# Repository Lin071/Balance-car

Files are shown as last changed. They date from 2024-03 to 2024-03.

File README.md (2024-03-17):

# Balance-car

本项目实现了两轮平衡小车，小车可利用遥控（安卓手机串口APP）进行操控（前后左右、灯光、蜂鸣器等）。该小车基于FreeRTOS，主控芯片采用STM32F103C8T6，其他模块包含：

- 一个MPU6050
- 一个OLED显示屏
- 两个蓝牙HC-05模块
- 两个直流减速电机（包含编码器）

PCB是采用Altium Designer设计的四层电路板，包含开关、稳压电路、按键、模块接口等，软件使用keil MDK开发。

# 系统流程

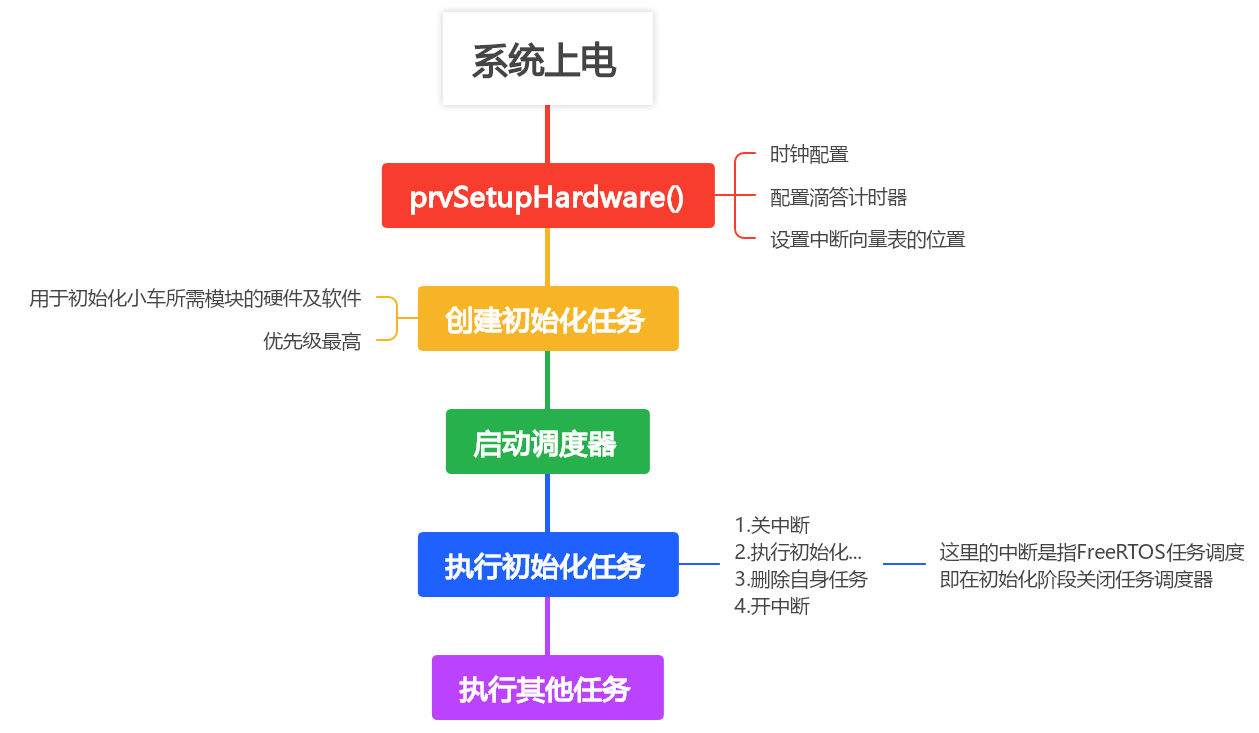
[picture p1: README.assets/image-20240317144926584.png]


小车系统上电后，首先执行FreeRTOS自带的硬件启动函数，包括时钟、中断向量表的地址配置等，使得FreeRTOS可以运行起来。

本项目会先创建一个任务，然后启动调度器。该任务用于初始化小车的各个模块以及创建其他任务，该任务完成后，会自己把自己删掉，起到一个初始化的作用。

- 那为什么要这样做呢？

  - 因为在一些模块的初始化，需要用到延迟函数（例如OLED），然后FreeRTOS已经使用了滴答计时器，这个时候就不好像裸机系统一样利用滴答计时器来计算延迟

  - 虽然说可以使用其他定时器或者纯软件实现延迟函数，但是这毕竟是需要消耗一些资源的，对于资源紧张的MCU来说成本就会增加

  - 正好FreeRTOS自带了ms级任务延迟，所以可以使用 `vTaskDelay(pdMS_TO_TICKS(xxx ms))` 函数来实现ms级延迟

  - 但是利用任务来初始化时一定要注意在任务延迟时，后台会将任务阻塞，为了避免在初始化任务中发生任务调度，需要关闭FreeRTOS的任务调度器

  - 初始化任务服务函数如下：

    ```c
    /***************************************************************************
    *函  数：static void vInitTask(void *pvParameters)
    *功  能：初始化任务，用于初始化小车模块以及创建其他模块
    *参  数：pvParameters 为创建任务时所传递的参数
    *返回值：无
    ***************************************************************************/
    static void vInitTask(void *pvParameters)
    {
    	taskENTER_CRITICAL();	//关闭任务调度
    
    	BaseType_t xReturn;
    	vTaskDelay(pdMS_TO_TICKS( 500UL ));		//先延迟一段时间
    	
    	NVIC_PriorityGroupConfig( NVIC_PriorityGroup_2 ); //设置NVIC中断分组2:2位抢占优先级，2位响应优先级
    
    	/*	相关模块初始化	*/
    	Led_Init();             //=====初始化与 LED 连接的IO
    	Beep_Init();			//=====初始化与 蜂鸣器 连接的IO
    	Key_Init();				//=====按键初始化
    	Oled_Init();			//=====OLED初始化
    	Motor_Init();		    //=====初始化与电机连接的硬件IO接口
    	Encoder_Init();       	//=====初始化编码器A
    	Uart1_init(115200);	    //=====串口1初始化(用于HC-05蓝牙连接上位机显示波形)
    	Uart3_init(115200);     //=====串口3初始化(用于手机遥控)
    	Mpu6050_Init();			//=====MPU6050初始化
    	Key_EXTI_Init();		//=====按键中断初始化
    	MPU6050_EXTI_Init();	//=====MPU6050中断初始化
    	xReturn = Task_Init();	//-----创建其他任务
    	
    	if (xReturn != pdPASS)
    		// 进入这里代表其他任务创建失败
    		OLED_ShowString(0,8,(u8 *)"Task init fail",16);
    
    	vTaskDelete(NULL); 	// 删除自己
    
    	taskEXIT_CRITICAL();	//打开任务调度
    }
    ```

在初始化任务完成之后，系统就会开始调度其他任务进行执行。

# 小车任务

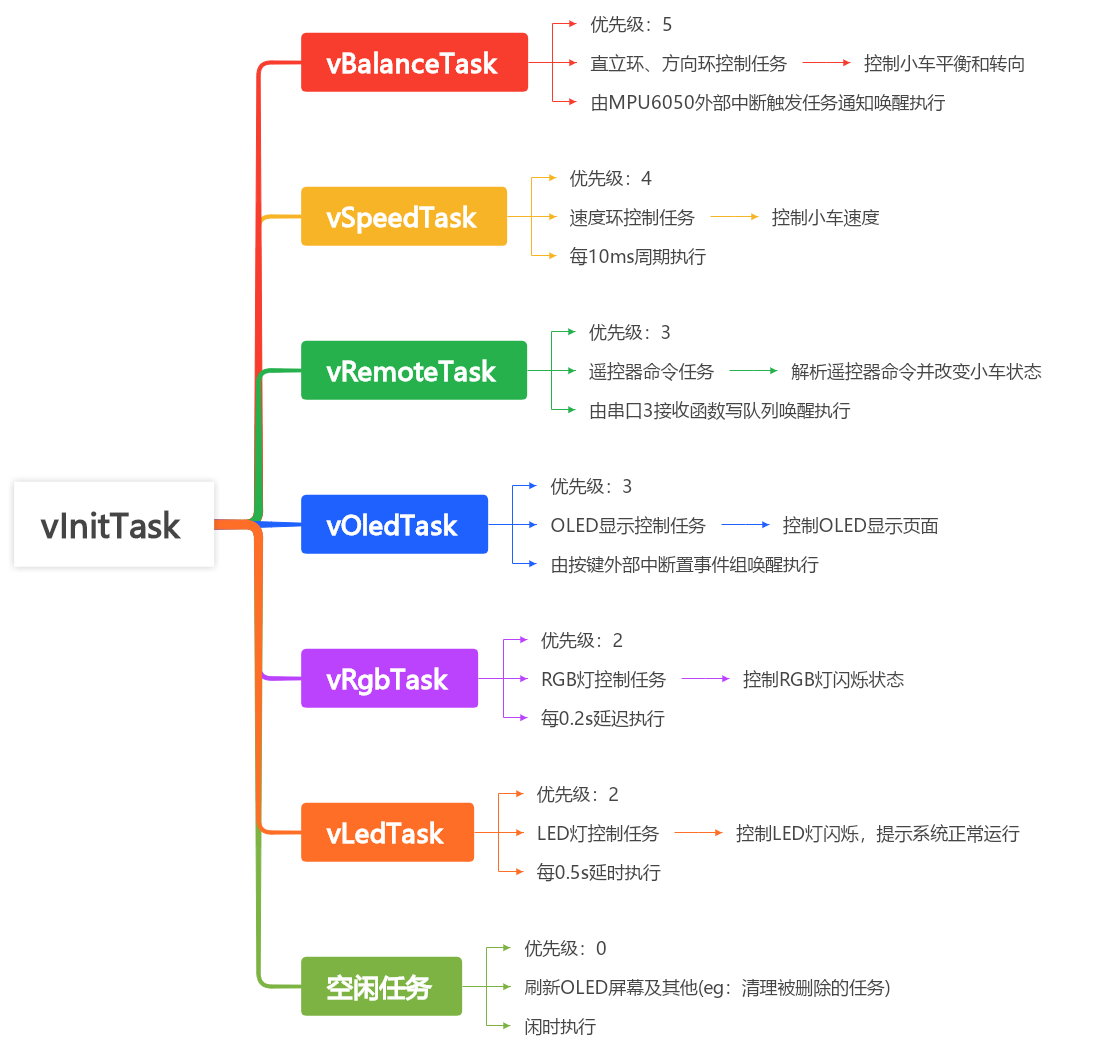
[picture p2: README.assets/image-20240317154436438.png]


本项目一共创建了8个任务，下面将依次介绍：

- `vInitTask`：第一个创建的任务，用于小车各个模块初始化、中断初始化以及创建其他任务，该任务只执行一次，执行完毕后立马删除自身
- `vBalanceTask`：控制小车直立和方向，内部使用任务通知阻塞等待MPU6050外部中断，只有得到了任务通知，该任务才可以执行
- `vSpeedTask`：控制小车速度，周期性获取小车编码器数值，并计算速度环控制输出
- `vRemoteTask`：解析遥控器命令，内部使用队列读阻塞等待，当队列中没有数据时阻塞，有数据时才会执行，队列数据由串口接收服务函数（接收遥控器命令）写入
- `vOledTask`：控制OLED屏幕的显示页面，内部使用事件组阻塞等待，当没有事件发生时阻塞，其中某个时间发生才会执行。事件由两个按键中断函数发出，一个按键代表页面前翻，一个代表页面后翻，即切换页面
- `vRgbTask`：控制RGB灯的状态，延时循环执行，根据用户发送过来的状态切换RGB灯状态（例如：跑马灯、红、黄、闪烁）
- `vLedTask`：控制LED灯翻转，延时循环执行，示意小车正常运行
- 空闲任务：用于CPU闲时处理其他不很重要事情，例如清理已被删除的任务、OLED屏幕刷新

# 任务执行条件

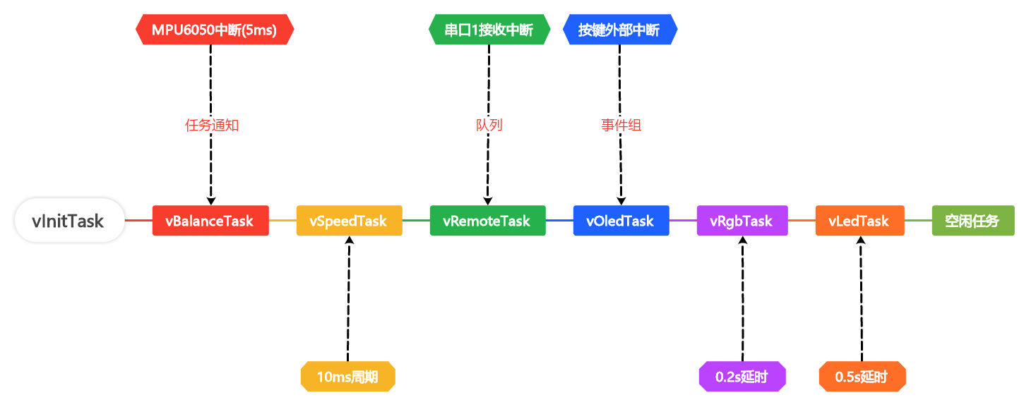
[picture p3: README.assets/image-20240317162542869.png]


# 中断优先级

本项目共用到了两类中断，5个中断：

- 串口1接收中断
- 串口3接收中断
- 按键1外部中断
- 按键2外部中断
- MPU6050数据外部中断

配置NVIC （NVIC的全称是Nested vectoredinterrupt controller，即嵌套向量中断控制器） 分组为 `NVIC_PriorityGroup_2` ，NVIC分组情况如下表所示：

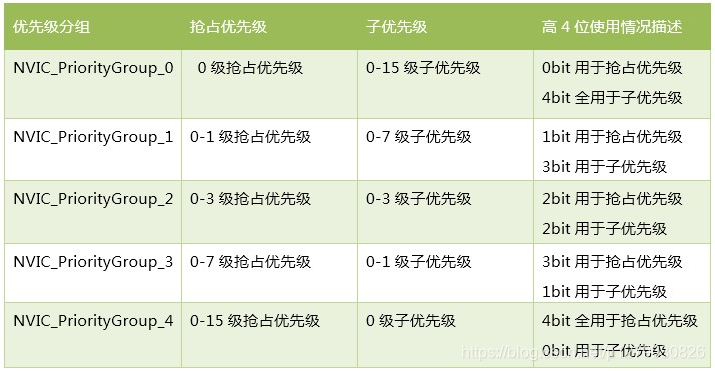
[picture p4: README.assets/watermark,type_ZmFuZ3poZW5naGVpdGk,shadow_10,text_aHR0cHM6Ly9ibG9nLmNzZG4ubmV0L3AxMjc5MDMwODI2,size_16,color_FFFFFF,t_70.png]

本项目各中断优先级配置如下：

| 中断名 | 抢占优先级 | 子优先级 |
| --- | --- | --- |
| MPU6050数据外部中断 | 0 | 1 |
| 按键1外部中断 | 1 | 1 |
| 按键2外部中断 | 1 | 2 |
| 串口1接收中断 | 2 | 1 |
| 串口3接收中断 | 2 | 2 |

另外，对于系统中断（比如：PendSV，SVC，SysTick）等优先级的配置见[FreeRTOS优先级配置说明](https://blog.csdn.net/p1279030826/article/details/103141778)

# 遇到的问题

## MPU6050初始化

- 问题描述：

  - 在初始化MPU6050时，总是会初始化不成功，或者是使用DAP调试器单步调试才能初始化成功，一旦使用电池供电就初始化失败！

- 可能的原因：

  - IIC时序出现问题，因为STM32F103芯片的硬件IIC可能会出现问题，所以本项目使用的是软件IIC，在将信号翻转的过程中，可能需要微秒级延迟一会，但是并没有实现

- 解决办法——实现微秒级延迟，采用方法：

  1. 使用纯软件的方式实现，即在延迟函数中不断进行一定次数循环，以满足特定的延迟时间。但是这种方法需要计算出每个循环所需要的时间，不同单片机的时钟主频不一致很难进行移植，而且延迟不也精准，何况还可能在for循环期间被RTOS任务切换，导致时间更加不准确，故不推荐使用这种方法。

     ```c
     // 实现微秒级延时
     static void delay_us(uint32_t nus)
     {
         uint32_t i;
         uint32_t time = xxx;	//每次循环所占的时间
         nus = nus * time;
         for (i = 0; i < nus; i++) {
             // 做一些其他事
         }
     }
     ```

  2. 使用滴答定时器方式实现微秒级延迟，虽然FreeRTOS是利用滴答定时器实现系统时间以及任务切换等等，但是这并不妨碍我们利用滴答计时器实现微秒级延迟。

     > 参考：https://www.iotword.com/17662.html

     ```c
     // 实现微秒级延时(在这之前一定要保证滴答定时器已经初始化了)
     void delay_us(uint32_t nus)
     {
         uint32_t ticks;
         uint32_t told, tnow, reload, tcnt = 0;
     
         reload = SysTick->LOAD;                    // 获取重装载寄存器值
         ticks = nus * (SystemCoreClock / 1000000); // 计数时间值（即需要延迟的tick数）
         told = SysTick->VAL;                       // 获取当前数值寄存器值（开始时数值）
     
         while (1)
         {
             tnow = SysTick->VAL; // 获取当前数值寄存器值
             if (tnow != told)    // 当前值不等于开始值说明已在计数
             {
                 if (tnow < told) {        // 当前值小于开始数值，说明未计到0
                     tcnt += told - tnow; // 计数值=开始值-当前值
                 } else {                              // 当前值大于开始数值，说明已计到0并重新计数
                     tcnt += reload - tnow + told; // 计数值=重装载值-当前值+开始值  （已从开始值计到0）
                 }
     
                 told = tnow; // 更新开始值
                 if (tcnt >= ticks) {
                     break; // 时间超过/等于要延迟的时间,则退出.
                 }
             }
         }
     }
     
     ```

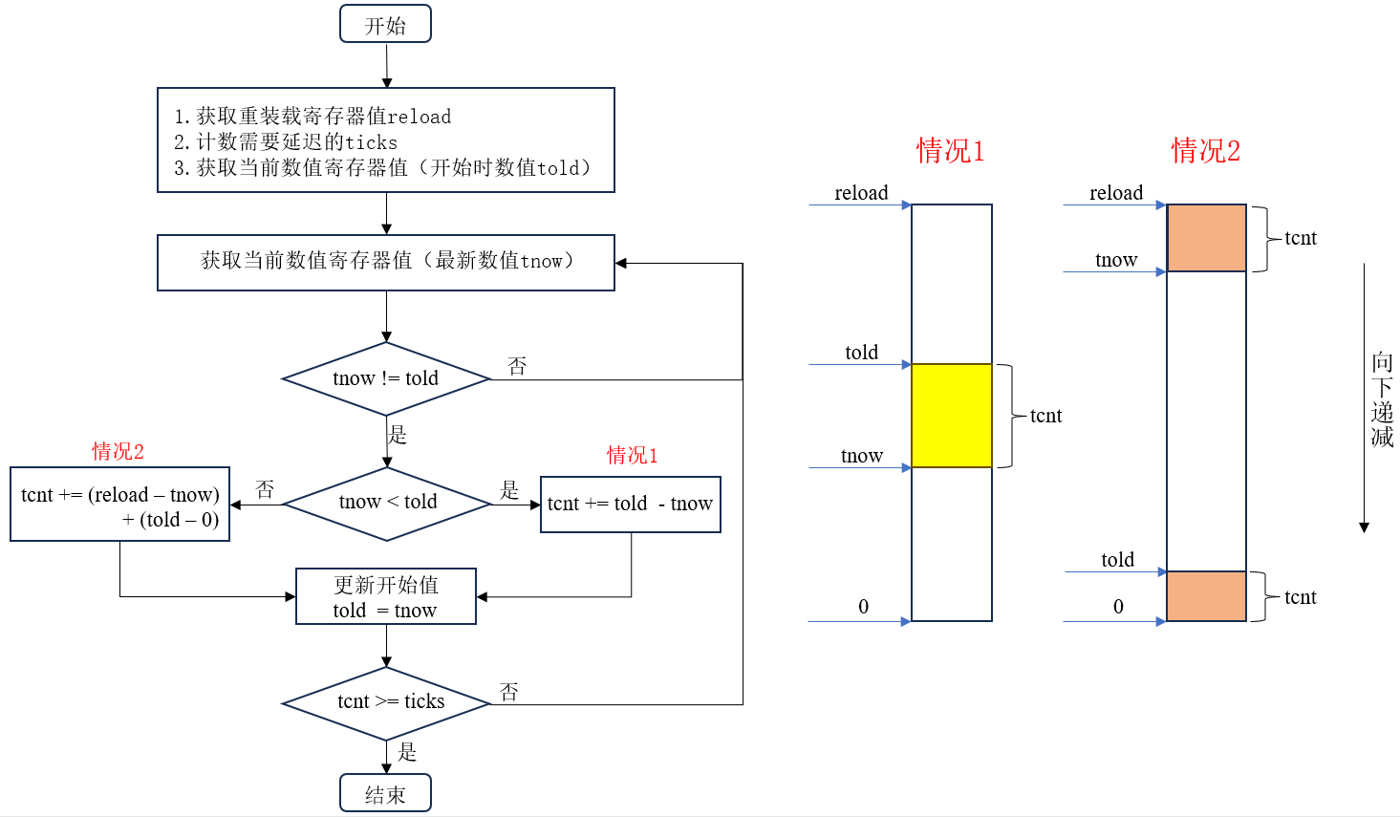
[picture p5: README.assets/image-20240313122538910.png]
     

  3. 使用定时器实现微秒级延迟，这种方法其实与上面第二种方法类似，只不过是换了一种定时器，原理也相同：

     1. 首先计算出需要延迟的时间对应的ticks
     2. 然后重新装载寄存器值
     3. 在循环里不断判断是否超出时间，一旦超出，立即退出

## 外部中断

- 问题描述：

  - 在开发过程中，想要使用按键来操控OLED屏幕显示不同的界面以及调试PID，但是在FreeRTOS中原来的轮循的方式不太行，于是想到使用按键的外部中断来获取按键值，然后在按键外部中断中使用事件组更改相应按键标志位，但是又和MPU6050的外部中断引脚共用了同一个外部中断线（EXTI_Line5）

  - 在STM32F103系列中，外部中断的共用资源主要包括：

    1. 不同端口、同一pin口，共用一个中断线：如PA1、PB1、PC1共用外部中断线1——EXTI_Line1，但是不可以同时使用
    2. 不同pin口、同一端口：这个都不用说，PA1、PA2、PA3这些共用的是同一个端口寄存器之类的
    3. 同一pin口共用一个中断线，但16个中断线却只共用7个中断服务函数：其中中断线EXTI_Line0-4独立拥有一个中断服务，中断线5-9共用一个中断服务函数，中断线10-15共用一个中断服务函数

    > [stm32共用外部中断线问题](https://blog.csdn.net/m0_65346989/article/details/129588667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)

  - 所以不可以同时使用 PA5(按键) 和 PB5(MPU6050) 来作为EXTI_Line5的外部中断

- 解决方案：

  - 只使用其中两个按键用于翻转OLED页面，去除原先的主页面，直接进入第一页面，然后根据按键切换上下页面
  - 至于PID等参数的调试，使用串口连接蓝牙，然后与手机连接，利用串口调试助手软件来更改PID的系数，以及控制小车

## 中断函数使用事件组

- 问题描述：

  - 这个问题是上面第二个问题的进一步延伸。使用其中两个按键来作为外部中断，一个按键按下表示OLED屏幕页面往前翻一页，另一个按键按下表示OLED屏幕往后翻一页
  - 为了更好地利用CPU，创建了一个空闲任务，在空闲任务不断刷新OLED屏幕，然后另外创建一个OLED控制任务，使用事件组来实现屏幕页面的切换
  - 当没有按键按下时，OLED屏幕控制任务处于阻塞态（即没有事件发生），当有时间发生时，判断是哪个事件（页面前翻或者后翻），根据事件类型来改变显示页面（改变函数指针）
  - 在按键中断中需要使用事件组发送事件，因为是外部中断属于ISR，所以需要使用 `xEventGroupSetBitsFromISR` 函数，但是编译的时候出现报错：未定义 `xTimerPendFunctionCallFromISR` 

- 解决方案：

  - 需要在 `FreeRTOSConfig.h` 定义以下：

    ```c
    #define INCLUDE_xEventGroupSetBitFromISR    1
    #define INCLUDE_xTimerPendFunctionCall  	1
    #define configUSE_TIMERS                	1
    ```

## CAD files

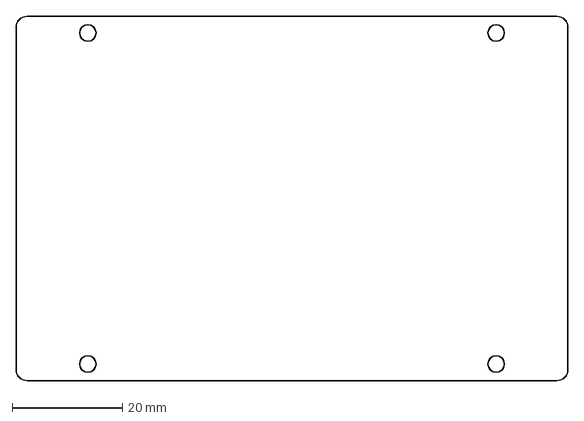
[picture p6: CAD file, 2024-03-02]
Pcb/板子形状.dxf
100.0 x 66.0 mm

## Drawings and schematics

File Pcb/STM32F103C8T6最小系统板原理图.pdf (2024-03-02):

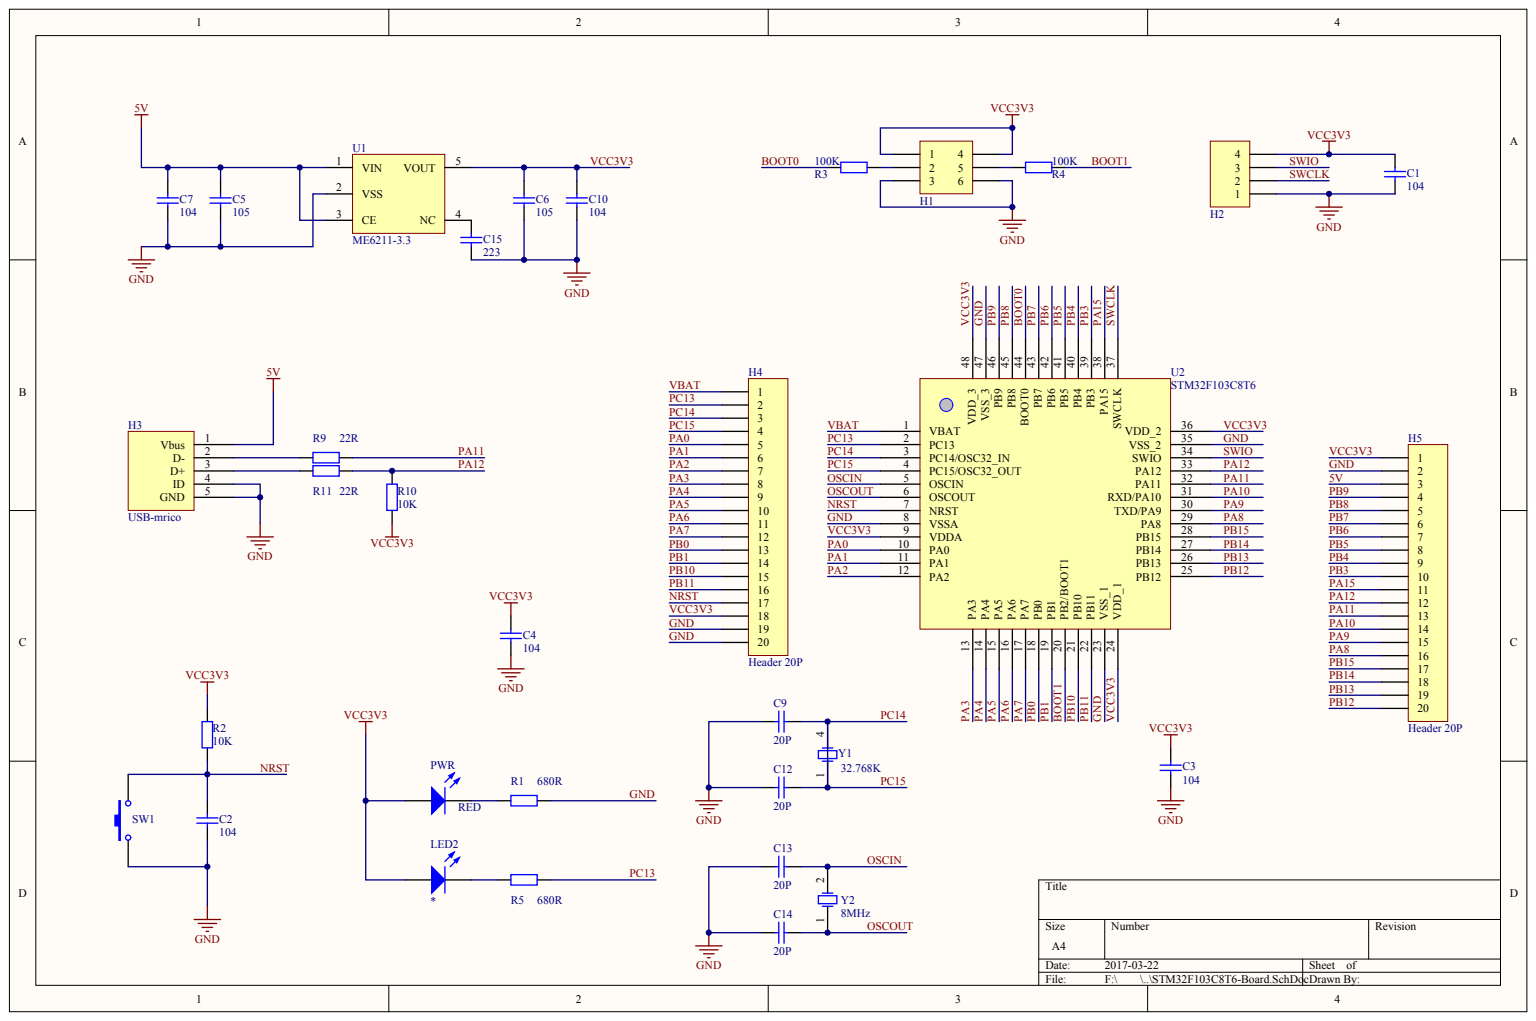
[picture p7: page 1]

VSS 2

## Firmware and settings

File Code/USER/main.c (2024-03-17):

/***********************************************************************/
//		    程序说明
//此程序用于：两轮平衡小车
//所用MCU芯片：STM32F103C8T6
//作者：071
//
/***********************************************************************/

#include "stm32f10x_rcc.h"

#include "FreeRTOS.h"
#include "timers.h"
#include "task.h"

#include "sys.h"
#include "led.h"
#include "beep.h"
#include "key.h"
#include "motor.h"
#include "encoder.h"
#include "oled.h"
#include "remote.h"
#include "control.h"
#include "mpu6050.h"




/* 硬件初始化函数声明 */
static void prvSetupHardware( void );
/*-----------------------------------------------------------*/



/***************************************************************************
*函  数：static void vInitTask(void *pvParameters)
*功  能：初始化任务，用于初始化小车模块以及创建其他模块
*参  数：pvParameters 为创建任务时所传递的参数
*返回值：无
***************************************************************************/
static void vInitTask(void *pvParameters)
{
	taskENTER_CRITICAL();	//关闭任务调度

	BaseType_t xReturn;
	vTaskDelay(pdMS_TO_TICKS( 500UL ));		//先延迟一段时间
	
	NVIC_PriorityGroupConfig( NVIC_PriorityGroup_2 ); //设置NVIC中断分组2:2位抢占优先级，2位响应优先级

	/*	相关模块初始化	*/
	Led_Init();             //=====初始化与 LED 连接的IO
	Beep_Init();			//=====初始化与 蜂鸣器 连接的IO
	Key_Init();				//=====按键初始化
	Oled_Init();			//=====OLED初始化
	Motor_Init();		    //=====初始化与电机连接的硬件IO接口
	Encoder_Init();       	//=====初始化编码器A
	Uart1_init(115200);	    //=====串口1初始化(用于HC-05蓝牙连接上位机显示波形)
	Uart3_init(115200);     //=====串口3初始化(用于手机遥控)
	Mpu6050_Init();			//=====MPU6050初始化
	Key_EXTI_Init();		//=====按键中断初始化
	MPU6050_EXTI_Init();	//=====MPU6050中断初始化
	xReturn = Task_Init();	//-----创建其他任务
	
	if (xReturn != pdPASS)
		// 进入这里代表其他任务创建失败
		OLED_ShowString(0,8,(u8 *)"Task init fail",16);

	vTaskDelete(NULL); 	// 删除自己

	taskEXIT_CRITICAL();	//打开任务调度
}



int main( void )
{
	BaseType_t xReturn;

 	/* RTOS所需基础硬件初始化 */
	prvSetupHardware();
	
  	/* 创建最初始的任务—————用于初始化小车其他模块以及创建其他任务 */
	xReturn = xTaskCreate(vInitTask, "InitTask", 500, NULL, 10, NULL);
	if (xReturn == pdPASS)
	{
		/* 启动调度器 */
		vTaskStartScheduler();
	}
		
	/* 如果程序运行到了这里就表示出错了, 一般是内存不足 */
	RGB_LED_Red();	//RGB红灯亮起
	BEEP_ON;		//蜂鸣器常鸣
	
	return 0;
}

/*-----------------------------------------------------------*/


/*-----------------------------------------------------------*/
static void prvSetupHardware( void )
{
	/* RCC（Reset and Clock Control）复位与时钟控制	Start with the clocks in their expected state. */
	RCC_DeInit();

	/* Enable HSE (high speed external clock). */
	RCC_HSEConfig( RCC_HSE_ON );

	/* Wait till HSE is ready. */
	while( RCC_GetFlagStatus( RCC_FLAG_HSERDY ) == RESET )
	{
	}

	/* 2 wait states required on the flash. */
	*( ( unsigned long * ) 0x40022000 ) = 0x02;

	/* HCLK = SYSCLK */
	RCC_HCLKConfig( RCC_SYSCLK_Div1 );

	/* PCLK2 = HCLK */
	RCC_PCLK2Config( RCC_HCLK_Div1 );

	/* PCLK1 = HCLK/2 */
	RCC_PCLK1Config( RCC_HCLK_Div2 );

	/* PLLCLK = 8MHz * 9 = 72 MHz. */
	RCC_PLLConfig( RCC_PLLSource_HSE_Div1, RCC_PLLMul_9 );

	/* Enable PLL. */
	RCC_PLLCmd( ENABLE );

	/* Wait till PLL is ready. */
	while(RCC_GetFlagStatus(RCC_FLAG_PLLRDY) == RESET)
	{
	}

	/* Select PLL as system clock source. */
	RCC_SYSCLKConfig( RCC_SYSCLKSource_PLLCLK );

	/* Wait till PLL is used as system clock source. */
	while( RCC_GetSYSCLKSource() != 0x08 )
	{
	}

	/* SPI2 Periph clock enable */
	RCC_APB1PeriphClockCmd( RCC_APB1Periph_SPI2, ENABLE );

	/* Configure HCLK clock as SysTick clock source. */
	SysTick_CLKSourceConfig( SysTick_CLKSource_HCLK );

	/* Set the Vector Table base address at 0x08000000 */
	NVIC_SetVectorTable( NVIC_VectTab_FLASH, 0x0 );	
}
/*-----------------------------------------------------------*/

#ifdef  DEBUG
/* Keep the linker happy. */
void assert_failed( unsigned char* pcFile, unsigned long ulLine )
{
	for( ;; )
	{
	}
}
#endif

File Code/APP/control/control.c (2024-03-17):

#include "control.h"

#include "FreeRTOS.h"
#include "event_groups.h"
#include "queue.h"


#include "led.h"
#include "mpu6050.h"
#include "motor.h"
#include "encoder.h"
#include "inv_mpu.h"
#include "oled.h"
#include "gui.h"
#include "remote.h"


// ==定义相关全局变量
PID balancePid, directionPid, speedPid;
float pitch, roll, yaw;
short gx, gy, gz;

// ===定义相关外部所需句柄
TaskHandle_t xBalanceTaskHandle;    // 直立环任务句柄
EventGroupHandle_t xEventGroup;     // 事件组句柄 
QueueHandle_t xQueue;               // 队列句柄


// ==定义任务句柄
static TaskHandle_t xLedTaskHandle;
static TaskHandle_t xRgbTaskHandle;
static TaskHandle_t xOledTaskHandle;
static TaskHandle_t xRemoteTaskHandle;
static TaskHandle_t xSpeedTaskHandle;



/***************************************************************************
*函  数：static void parameterInit(void)
*功  能：PID等参数初始化
*参  数：无
*返回值：无
***************************************************************************/
static void parameterInit(void)
{
    // PID系数初始化
    balancePid.expect = -7.5f;
    balancePid.Kp = 465.0f;       // 0 ~ 700 
    balancePid.Ki = 0.0f;
    balancePid.Kd = -0.55f;

    directionPid.expect = 0;
    directionPid.Kp = 0.65f;
    directionPid.Ki = 0.0f;
    directionPid.Kd = 0.0f;

    speedPid.expect = 0;
    speedPid.Kp = 13.0f;
    speedPid.Ki = 0.065f;
    speedPid.Kd = 0.0f;
}


/***************************************************************************
*函  数：void vApplicationIdleHook(void)
*功  能：空闲任务钩子函数————(优先级最低：0     该任务不可以阻塞)
        1、处理被删除的任务
        2、刷新OLED屏幕
*参  数：pvParameters 为创建任务时所传递的参数
*返回值：无
***************************************************************************/
void vApplicationIdleHook(void)
{
    OLED_Clear();
    pPage();        // 刷新OLED屏幕
}


/***************************************************************************
*函  数：static void vLedTask(void *pvParameters)
*功  能：LED灯任务，闪烁LED灯，提示小车正常运行
*参  数：pvParameters 为创建任务时所传递的参数
*返回值：无
***************************************************************************/
static void vLedTask(void *pvParameters)
{
    const TickType_t xDelayTicks = pdMS_TO_TICKS(500UL);
    uint8_t cnt = 0;
    
    while(1)
    {
        cnt++;
        if(cnt%2 == 0)      // 翻转LED
            LED_OFF;
        else
            LED_ON;
        
        /* 延时 */
        vTaskDelay(xDelayTicks);
    }
}



/***************************************************************************
*函  数：static void vRgbTask(void *pvParameters)
*功  能：RGB灯任务，控制RGB灯的行为，使小车更具趣味性
*参  数：pvParameters 为创建任务时所传递的参数
*返回值：无
***************************************************************************/
static void vRgbTask(void *pvParameters)
{
    const TickType_t xDelayTicks = pdMS_TO_TICKS(200UL);
    
    while(1)
    {
        // 根据rgbState标志位选择RGB状态
        switch(remoteState.rgbState)
        {
            case RGB_OFF:
                RGB_LED_Off();
                break;
            case RGB_FLY:
                RGB_LED_FLY();
                break;
            case RGB_RUNNING:
                RGB_LED_Runing();
                break;
            case RGB_RED:
                RGB_LED_Red();
                break;
            case RGB_BLUE:
                RGB_LED_Blue();
                break;
            case RGB_YELLOW:
                RGB_LED_Yellow();
                break;
            case RGB_WHITE:
                RGB_LED_White();
                break;     
        }

        /* 延时 */
        vTaskDelay(xDelayTicks);
    }
}



/***************************************************************************
*函  数：static void vOledTask(void *pvParameters)
*功  能：OLED显示控制任务，用于控制OLED显示的内容
*参  数：pvParameters 为创建任务时所传递的参数
*返回值：无
***************************************************************************/
static void vOledTask(void *pvParameters)
{
    const TickType_t xDelayTicks = pdMS_TO_TICKS(20UL);
    int8_t i = 0;
    EventBits_t xReturnBit;
    Page_Init();    // 初始化屏幕显示页
    
    while(1)
    {
        /* 延时 */
        vTaskDelay(xDelayTicks);

        /* 等待某一个按键，获取事件后清除标志位，无限期阻塞 */
		xReturnBit = xEventGroupWaitBits(xEventGroup, UP|DOWN, pdTRUE, pdFALSE, portMAX_DELAY);

        // 根据返回值判断哪个按键按下
        if (xReturnBit == UP)
        {
            i--;
            i = i < 0 ? 0 : i;      // 限幅
        } else if (xReturnBit == DOWN)
        {
            i++;
            i = i > (ARR_SIZE-1) ? (ARR_SIZE-1) : i;    // 限幅
        }

        pPage = pageFunctions[i];   // 更新页面
    }
}


/***************************************************************************
*函  数：static void vRemoteTask(void *pvParameters)
*功  能：解析遥控命令任务，等待串口3发送数据至队列，不断读取队列数据
*参  数：pvParameters 为创建任务时所传递的参数
*返回值：无
***************************************************************************/
static void vRemoteTask(void *pvParameters)
{
    uint8_t receivedValue;
    BaseType_t xStatus;

    while(1)
    {
        /* 读取从手机遥控端发送过来的消息，即读取队列
         * 从 xQueue 队列中读取数据至 receivedValue 变量，如果队列没有数据，则无限阻塞
         */
        xStatus = xQueueReceive( xQueue, &receivedValue, portMAX_DELAY);

        // 判断是否读到了数据
        if (xStatus == pdPASS)
        {   
            // 带入解析
            Bluetooth_Receive_Parsing(receivedValue);
        }
    }
}



/***************************************************************************
*函  数：static void vBalanceTask(void *pvParameters)
*功  能：直立环控制任务
*参  数：pvParameters 为创建任务时所传递的参数
*返回值：无
***************************************************************************/
static void vBalanceTask(void *pvParameters)
{
    parameterInit();

    while(1)
    {
        /* 阻塞等待MPU6050中断任务通知，被通知后将通知值清零 */
        ulTaskNotifyTake(pdTRUE, portMAX_DELAY);

        MPU_Get_Gyroscope(&gx, &gy, &gz);         //===得到角速度的数据
        mpu_dmp_get_data(&pitch, &roll, &yaw);    //===得到欧拉角（姿态角）的数据

        // 直立环代码...
        balancePid.error = balancePid.expect - pitch;
        balancePid.out = (int16_t)(balancePid.Kp*balancePid.error + balancePid.Kd*gy);

        // 方向环代码...
        directionPid.error = directionPid.expect - gz;
        directionPid.out = (int16_t)(directionPid.Kp*directionPid.error);

        /* 改变左右两轮占空比 */
        // setMotorPwm(balancePid.out + speedPid.out - directionPid.out, balancePid.out + speedPid.out + directionPid.out);
        setMotorPwm(0, 0);
    }
}
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

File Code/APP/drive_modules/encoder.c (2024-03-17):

#include "encoder.h"

#include <stdio.h>
#include <stdint.h>

#include "stm32f10x_tim.h"
#include "stm32f10x_gpio.h"
#include "stm32f10x_rcc.h"

#include "control.h"


/**************************************************************************
函数功能：把TIM2初始化为编码器接口模式（读取左车轮编码速度）
入口参数：无
返回  值：无
**************************************************************************/
static void A_Encoder_Init(void)
{
	TIM_TimeBaseInitTypeDef TIM_TimeBaseStructure;  
	TIM_ICInitTypeDef TIM_ICInitStructure;  
	GPIO_InitTypeDef GPIO_InitStructure;
	RCC_APB1PeriphClockCmd(RCC_APB1Periph_TIM2, ENABLE);	//使能定时器2的时钟
	RCC_APB2PeriphClockCmd(RCC_APB2Periph_GPIOA, ENABLE);	//使能PA端口时钟
		
	GPIO_InitStructure.GPIO_Pin = GPIO_Pin_0|GPIO_Pin_1;	//端口配置(PA0\PA1)
	GPIO_InitStructure.GPIO_Mode = GPIO_Mode_IN_FLOATING; 	//浮空输入
	GPIO_Init(GPIOA, &GPIO_InitStructure);					//根据设定参数初始化GPIOA
	
	TIM_TimeBaseStructInit(&TIM_TimeBaseStructure);
	TIM_TimeBaseStructure.TIM_Prescaler = 0x0; // 预分频器
	TIM_TimeBaseStructure.TIM_Period = ENCODER_TIM_PERIOD; 		//设定计数器自动重装值
	TIM_TimeBaseStructure.TIM_ClockDivision = TIM_CKD_DIV1;		//选择时钟分频：不分频
	TIM_TimeBaseStructure.TIM_CounterMode = TIM_CounterMode_Up;	//TIM向上计数  
	TIM_TimeBaseInit(TIM2, &TIM_TimeBaseStructure);
	TIM_EncoderInterfaceConfig(TIM2, TIM_EncoderMode_TI12, TIM_ICPolarity_Rising, TIM_ICPolarity_Rising);	//使用编码器模式3
	TIM_ICStructInit(&TIM_ICInitStructure);
	TIM_ICInitStructure.TIM_ICFilter = 10;
	TIM_ICInit(TIM2, &TIM_ICInitStructure);
	TIM_ClearFlag(TIM2, TIM_FLAG_Update);	//清除TIM的更新标志位
	TIM_ITConfig(TIM2, TIM_IT_Update, ENABLE);
	//Reset counter
	TIM_SetCounter(TIM2,0);
	TIM_Cmd(TIM2, ENABLE); 
}

/**************************************************************************
函数功能：把TIM4初始化为编码器接口模式（读取右车轮编码速度）
入口参数：无
返回  值：无
**************************************************************************/
static void B_Encoder_Init(void)
{
	TIM_TimeBaseInitTypeDef TIM_TimeBaseStructure;  
	TIM_ICInitTypeDef TIM_ICInitStructure;  
	GPIO_InitTypeDef GPIO_InitStructure;
	RCC_APB1PeriphClockCmd(RCC_APB1Periph_TIM4, ENABLE);//使能定时器4的时钟
	RCC_APB2PeriphClockCmd(RCC_APB2Periph_GPIOB, ENABLE);//使能PB端口时钟
	
	GPIO_InitStructure.GPIO_Pin = GPIO_Pin_6|GPIO_Pin_7;	//端口配置(PTB6\PTB7)
	GPIO_InitStructure.GPIO_Mode = GPIO_Mode_IN_FLOATING; //浮空输入
	GPIO_Init(GPIOB, &GPIO_InitStructure);					      //根据设定参数初始化GPIOB
	
	TIM_TimeBaseStructInit(&TIM_TimeBaseStructure);
	TIM_TimeBaseStructure.TIM_Prescaler = 0x0; // 预分频器 
	TIM_TimeBaseStructure.TIM_Period = ENCODER_TIM_PERIOD; //设定计数器自动重装值
	TIM_TimeBaseStructure.TIM_ClockDivision = TIM_CKD_DIV1;//选择时钟分频：不分频
	TIM_TimeBaseStructure.TIM_CounterMode = TIM_CounterMode_Up;////TIM向上计数  
	TIM_TimeBaseInit(TIM4, &TIM_TimeBaseStructure);
	TIM_EncoderInterfaceConfig(TIM4, TIM_EncoderMode_TI12, TIM_ICPolarity_Rising, TIM_ICPolarity_Rising);//使用编码器模式3
	TIM_ICStructInit(&TIM_ICInitStructure);
	TIM_ICInitStructure.TIM_ICFilter = 10;
	TIM_ICInit(TIM4, &TIM_ICInitStructure);
	TIM_ClearFlag(TIM4, TIM_FLAG_Update);//清除TIM的更新标志位
	TIM_ITConfig(TIM4, TIM_IT_Update, ENABLE);
	//Reset counter
	TIM_SetCounter(TIM4,0);
	TIM_Cmd(TIM4, ENABLE); 
}


/**************************************************************************
函数功能：初始化小车TIM2和TIM4，用于读取小车的编码器转速
入口参数：无
返回  值：无
**************************************************************************/
void Encoder_Init(void)
{
	A_Encoder_Init();	//初始化左轮编码器定时器TIM2
	B_Encoder_Init();	//初始化右轮编码器定时器TIM4
}


/**************************************************************************
函数功能：TIM4中断服务函数
入口参数：无
返回  值：无
**************************************************************************/
void TIM4_IRQHandler(void)
{ 		    		  			    
	if(TIM4->SR&0X0001)//溢出中断
	{    				   				     	    	
	}				   
	TIM4->SR&=~(1<<0);//清除中断标志位 	    
}

/**************************************************************************
函数功能：TIM2中断服务函数
入口参数：无
返回  值：无
**************************************************************************/
void TIM2_IRQHandler(void)
{ 		    		  			    
	if(TIM2->SR&0X0001)//溢出中断
	{    				   				     	    	
	}				   
	TIM2->SR&=~(1<<0);//清除中断标志位 	    
}

/**************************************************************************
函数功能：单位时间读取编码器计数
入口参数：定时器
返回  值：速度值
**************************************************************************/
static int16_t Read_Encoder(uint8_t TIMX)
{
	 int16_t Encoder_TIM;    
	 switch(TIMX)
	 {
		 case 2:  Encoder_TIM = (short)TIM2 -> CNT;  TIM2 -> CNT=0; break;
		 case 3:  Encoder_TIM = (short)TIM3 -> CNT;  TIM3 -> CNT=0; break;	
		 case 4:  Encoder_TIM = (short)TIM4 -> CNT;  TIM4 -> CNT=0; break;	
		 default: Encoder_TIM = 0;
	 }
	 return Encoder_TIM;
}

/**************************************************************************
函数功能：获取左右两轮的速度
入口参数：传入一个指针，用于读取速度
返回  值：空
**************************************************************************/
void getSpeed(int16_t *p_leftEncoder,int16_t *p_rightEncoder)
{
    *p_leftEncoder = Read_Encoder(2);
    *p_rightEncoder = -Read_Encoder(4);
}


/**************************************************************************
函数功能：测试TIM2\TIM4读取编码器功能函数
入口参数：无
返回  值：无
**************************************************************************/
void Encoder_TIM_Test(void)
{
	int16_t Encoder_A = 0;
	int16_t Encoder_B = 0;

	Encoder_A = Read_Encoder(2);
	Encoder_B = -Read_Encoder(4);

	printf("d:%d,%d\n",Encoder_A,Encoder_B);
}

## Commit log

2024-03-02 第一次上传
    [原理图.SchDoc, 板子形状.dxf]
2024-03-02 添加了FreeRTOS代码
2024-03-03 增加了FreeRTOS配置头文件
2024-03-03 修改了启动文件，导入并替换成FreeRTOS的中断函数
2024-03-17 添加了项目说明
2024-03-17 更新了整个工程代码
